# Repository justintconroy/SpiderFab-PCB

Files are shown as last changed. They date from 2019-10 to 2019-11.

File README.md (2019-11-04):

# SpiderFab Control Board

This board is made to control [SpiderFab](https://github.com/justintconroy/SpiderFab).

It's mostly just my attempts to learn how to make PCBs using EAGLE.
Version 1.0 supports:
* 2.3-16V battery power supply
* 1000mAh charger for internal LiPo battery
* Charge via USB or 5mm barrel connector
* 12 servos
* 2 DC motors

# Next version
I'm already thinking of what I might change on this to make it more
generally useful. Potential changes:
* Add a [GPIO expander](https://www.mouser.com/ProductDetail/NXP-Semiconductors/PCA9685PW118?qs=sGAEpiMZZMvKM5ialpXrmnWDpPMxsdrM)
  to support more actuators.
* Switch to an SMT version of the motor driver to make some more space
  on the board. (might be a bad idea if we want to make it easy to
  replace burned out drivers by socketing them).
* Add another motor driver to allow controlling 4 motors.

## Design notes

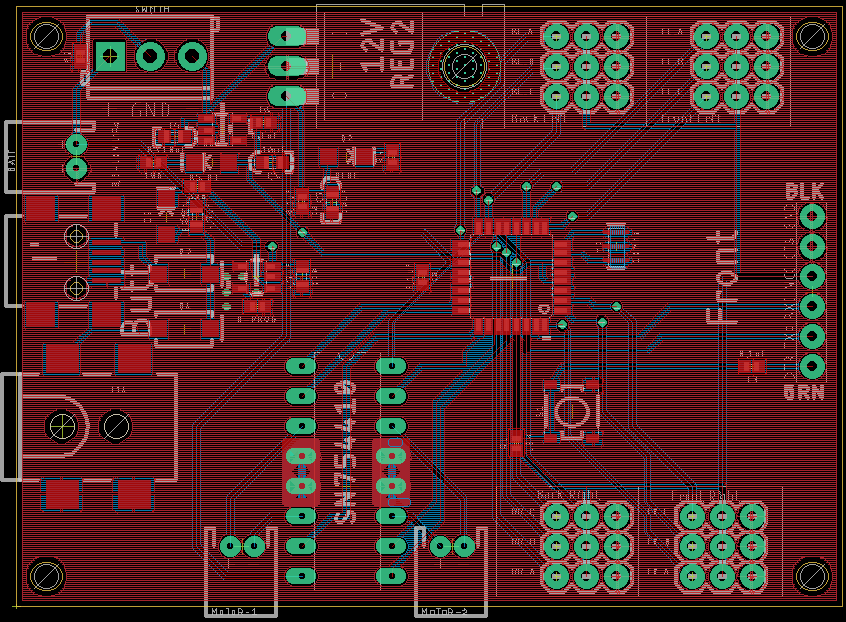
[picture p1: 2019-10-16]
SpiderFab_Board_Front.png

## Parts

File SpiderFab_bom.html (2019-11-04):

Qty | Value | Device | Package | Parts | Description | DESIGNER | PROD_ID | SF_ID | SKU | VALUE | VERSION
1 |  | 6_PIN_SERIAL_TARGETSILK | 6_PIN_SERIAL_TARGET_SIDE_W_SILK | J1 | 6-pin header connection for use with the "FTDI BASIC" pinout - TARGET SIDE.
2 |  | CONN_02JST-PTH-2 | JST-2-PTH | MOTOR-1, MOTOR-2 | Multi connection point. Often used as Generic Header-pin footprint for 0.1 inch spaced/style header connections |  | CONN-09863 |  | PRT-09914
12 |  | CONN_03 | 1X03 | BL_A, BL_B, BL_C, BR_A, BR_B, BR_C, FL_A, FL_B, FL_C, FR_A, FR_B, FR_C | Multi connection point. Often used as Generic Header-pin footprint for 0.1 inch spaced/style header connections
1 |  | CONN_03SCREW | SCREWTERMINAL-3.5MM-3 | SWITCH | Multi connection point. Often used as Generic Header-pin footprint for 0.1 inch spaced/style header connections |  | CONN-08288 | PRT-08235
2 |  | RESISTOR0402 | 0402 | R2, R4 | Generic Resistor Package
4 | 0.1uF | 0.1UF-0402-16V-10% | 0402 | C2, C3, C6, C8 | 0.1µF ceramic capacitors |  | CAP-12416 |  |  | 0.1uF
2 | 10K | RESISTOR0402 | 0402 | R1, R3 | Generic Resistor Package
3 | 10uF | 10UF-POLAR-0603-6.3V-20%(TANT) | 0603-POLAR | C4, C5, C7 | 10.0µF polarized capacitors |  | CAP-13210 |  |  | 10uF
1 | 12V | V_REG_78XX-TO-220 | TO-220-ALT | REG2 | Voltage Regulator |  | VREG-08450 | COM-00107
1 | 16MHz | RESONATOR-16MHZSMD_3.2X1.3 | RESONATOR-SMD-3.2X1.3 | Y1 | 16MHz Resonator |  | XTAL-08900 |  |  | 16MHz
2 | 1A/40V/500mV | DIODE-SCHOTTKY-SS14 | SMA-DIODE | D3, D4 | Schottky diode |  | DIO-08053 |  |  | 1A/40V/500mV
1 | 1K | RESISTOR0402 | 0402 | R-PROG | Generic Resistor Package
1 | 3.3-16V LiPo | CONN_02JST-PTH-2 | JST-2-PTH | BATT | Multi connection point. Often used as Generic Header-pin footprint for 0.1 inch spaced/style header connections |  | CONN-09863 |  | PRT-09914
1 | 3.3V/150mA | V_REG_MIC52053.3V | SOT23-5 | REG1 | V_REG MIC5205 Standard 3.3V, 5V, and Adjustable 150mA LDO voltage regulator in SOT-23 layout. Micrel part MIC5205. BP (by-pass) pin is used to lower output noise with 470pF cap, may be left open. On the adjustable version BP is used to set output. |  | VREG-00822 |  |  | 3.3V/150mA
1 | 330 | RESISTOR0402 | 0402 | R5 | Generic Resistor Package
2 | 4.7uF | 4.7UF0603 | 0603 | C9, C10 | 4.7µF ceramic capacitors |  | CAP-08280 |  |  | 4.7uF
1 | 5.5x2.1mm Barrel | POWER_JACKSMD | POWER_JACK_SMD | J14 | Power Jack Connector |  | CONN-08106 | PRT-12748 |  | 5.5x2.1mm Barrel
1 | ATMEGA328 | ATMEGA168 | TQFP32-08 | U1
1 | BLUE | LED1206 | LED-1206 | D2 | LED (Generic)
1 | FRAME-LETTERNO_PACKAGE | FRAME-LETTERNO_PACKAGE | DUMMY | FRAME1 | Schematic Frame - Letter | Justin T. Conroy |  |  |  |  | v01
1 | GREEN | LED1206 | LED-1206 | D5 | LED (Generic)
1 | MCP73831 | MCP73831 | SOT23-5 | U3 | Miniature single cell, fully integrated Li-Ion, Li-polymer charge management controller |  | IC-09995
1 | MOMENTARY-SWITCH-SPST-SMD-4.5MM | MOMENTARY-SWITCH-SPST-SMD-4.5MM | TACTILE_SWITCH_SMD_4.5MM | S1 | Momentary Switch (Pushbutton) - SPST |  | SWCH-09213
1 | RED | LED1206 | LED-1206 | D1 | LED (Generic)
1 | SN754410 | SN754410 | DIP16 | IC1 | Quadruple half-H driver
1 | USBSMD | USBSMD | USB-MINIB | X1 | USB Connectors

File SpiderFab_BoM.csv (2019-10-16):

Part | Value | Device | Package | Description | DESIGNER | PROD_ID | SF_ID | SKU | VALUE | VERSION
BATT | 3.3-16V LiPo | CONN_02JST-PTH-2 | JST-2-PTH | Multi connection point. Often used as Generic Header-pin footprint for 0.1 inch spaced/style header connections |  | CONN-09863 |  | PRT-09914
BL_A |  | CONN_03 | 1X03 | Multi connection point. Often used as Generic Header-pin footprint for 0.1 inch spaced/style header connections
BL_B |  | CONN_03 | 1X03 | Multi connection point. Often used as Generic Header-pin footprint for 0.1 inch spaced/style header connections
BL_C |  | CONN_03 | 1X03 | Multi connection point. Often used as Generic Header-pin footprint for 0.1 inch spaced/style header connections
BR_A |  | CONN_03 | 1X03 | Multi connection point. Often used as Generic Header-pin footprint for 0.1 inch spaced/style header connections
BR_B |  | CONN_03 | 1X03 | Multi connection point. Often used as Generic Header-pin footprint for 0.1 inch spaced/style header connections
BR_C |  | CONN_03 | 1X03 | Multi connection point. Often used as Generic Header-pin footprint for 0.1 inch spaced/style header connections
C2 | 0.1uF | 0.1UF-0402-16V-10% | 0402 | 0.1µF ceramic capacitors |  | CAP-12416 |  |  | 0.1uF
C3 | 0.1uF | 0.1UF-0402-16V-10% | 0402 | 0.1µF ceramic capacitors |  | CAP-12416 |  |  | 0.1uF
C4 | 10uF | 10UF-POLAR-0603-6.3V-20%(TANT) | 0603-POLAR | 10.0µF polarized capacitors |  | CAP-13210 |  |  | 10uF
C5 | 10uF | 10UF-POLAR-0603-6.3V-20%(TANT) | 0603-POLAR | 10.0µF polarized capacitors |  | CAP-13210 |  |  | 10uF
C6 | 0.1uF | 0.1UF-0402-16V-10% | 0402 | 0.1µF ceramic capacitors |  | CAP-12416 |  |  | 0.1uF
C7 | 10uF | 10UF-POLAR-0603-6.3V-20%(TANT) | 0603-POLAR | 10.0µF polarized capacitors |  | CAP-13210 |  |  | 10uF
C8 | 0.1uF | 0.1UF-0402-16V-10% | 0402 | 0.1µF ceramic capacitors |  | CAP-12416 |  |  | 0.1uF
C9 | 4.7uF | 4.7UF0603 | 0603 | 4.7µF ceramic capacitors |  | CAP-08280 |  |  | 4.7uF
C10 | 4.7uF | 4.7UF0603 | 0603 | 4.7µF ceramic capacitors |  | CAP-08280 |  |  | 4.7uF
D1 | RED | LED1206 | LED-1206 | LED (Generic)
D2 | BLUE | LED1206 | LED-1206 | LED (Generic)
D3 | 1A/40V/500mV | DIODE-SCHOTTKY-SS14 | SMA-DIODE | Schottky diode |  | DIO-08053 |  |  | 1A/40V/500mV
D4 | 1A/40V/500mV | DIODE-SCHOTTKY-SS14 | SMA-DIODE | Schottky diode |  | DIO-08053 |  |  | 1A/40V/500mV
D5 | GREEN | LED1206 | LED-1206 | LED (Generic)
FL_A |  | CONN_03 | 1X03 | Multi connection point. Often used as Generic Header-pin footprint for 0.1 inch spaced/style header connections
FL_B |  | CONN_03 | 1X03 | Multi connection point. Often used as Generic Header-pin footprint for 0.1 inch spaced/style header connections
FL_C |  | CONN_03 | 1X03 | Multi connection point. Often used as Generic Header-pin footprint for 0.1 inch spaced/style header connections
FRAME1 | FRAME-LETTERNO_PACKAGE | FRAME-LETTERNO_PACKAGE | DUMMY | Schematic Frame - Letter | Justin T. Conroy |  |  |  |  | v01
FR_A |  | CONN_03 | 1X03 | Multi connection point. Often used as Generic Header-pin footprint for 0.1 inch spaced/style header connections
FR_B |  | CONN_03 | 1X03 | Multi connection point. Often used as Generic Header-pin footprint for 0.1 inch spaced/style header connections
FR_C |  | CONN_03 | 1X03 | Multi connection point. Often used as Generic Header-pin footprint for 0.1 inch spaced/style header connections
IC1 | SN754410 | SN754410 | DIP16 | Quadruple half-H driver
J1 |  | 6_PIN_SERIAL_TARGETSILK | 6_PIN_SERIAL_TARGET_SIDE_W_SILK | 6-pin header connection for use with the FTDI BASIC" pinout - TARGET SIDE."
J14 | 5.5x2.1mm Barrel | POWER_JACKSMD | POWER_JACK_SMD | Power Jack Connector |  | CONN-08106 | PRT-12748 |  | 5.5x2.1mm Barrel
MOTOR-1 |  | CONN_02JST-PTH-2 | JST-2-PTH | Multi connection point. Often used as Generic Header-pin footprint for 0.1 inch spaced/style header connections |  | CONN-09863 |  | PRT-09914
MOTOR-2 |  | CONN_02JST-PTH-2 | JST-2-PTH | Multi connection point. Often used as Generic Header-pin footprint for 0.1 inch spaced/style header connections |  | CONN-09863 |  | PRT-09914
R-PROG | 1K | RESISTOR0402 | 0402 | Generic Resistor Package
R1 | 10K | RESISTOR0402 | 0402 | Generic Resistor Package
R2 |  | RESISTOR0402 | 0402 | Generic Resistor Package
R3 | 10K | RESISTOR0402 | 0402 | Generic Resistor Package
R4 |  | RESISTOR0402 | 0402 | Generic Resistor Package
R5 | 330 | RESISTOR0402 | 0402 | Generic Resistor Package
REG1 | 3.3V/150mA | V_REG_MIC52053.3V | SOT23-5 | V_REG MIC5205 Standard 3.3V, 5V, and Adjustable 150mA LDO voltage regulator in SOT-23 layout. Micrel part MIC5205. BP (by-pass) pin is used to lower output noise with 470pF cap, may be left open. On the adjustable version BP is used to set output. |  | VREG-00822 |  |  | 3.3V/150mA
REG2 | 12V | V_REG_78XX-TO-220 | TO-220-ALT | Voltage Regulator |  | VREG-08450 | COM-00107
S1 | MOMENTARY-SWITCH-SPST-SMD-4.5MM | MOMENTARY-SWITCH-SPST-SMD-4.5MM | TACTILE_SWITCH_SMD_4.5MM | Momentary Switch (Pushbutton) - SPST |  | SWCH-09213
SWITCH |  | CONN_03SCREW | SCREWTERMINAL-3.5MM-3 | Multi connection point. Often used as Generic Header-pin footprint for 0.1 inch spaced/style header connections |  | CONN-08288 | PRT-08235
U1 | ATMEGA328 | ATMEGA168 | TQFP32-08
U3 | MCP73831 | MCP73831 | SOT23-5 | Miniature single cell, fully integrated Li-Ion, Li-polymer charge management controller |  | IC-09995
X1 | USBSMD | USBSMD | USB-MINIB | USB Connectors
Y1 | 16MHz | RESONATOR-16MHZSMD_3.2X1.3 | RESONATOR-SMD-3.2X1.3 | 16MHz Resonator |  | XTAL-08900 |  |  | 16MHz

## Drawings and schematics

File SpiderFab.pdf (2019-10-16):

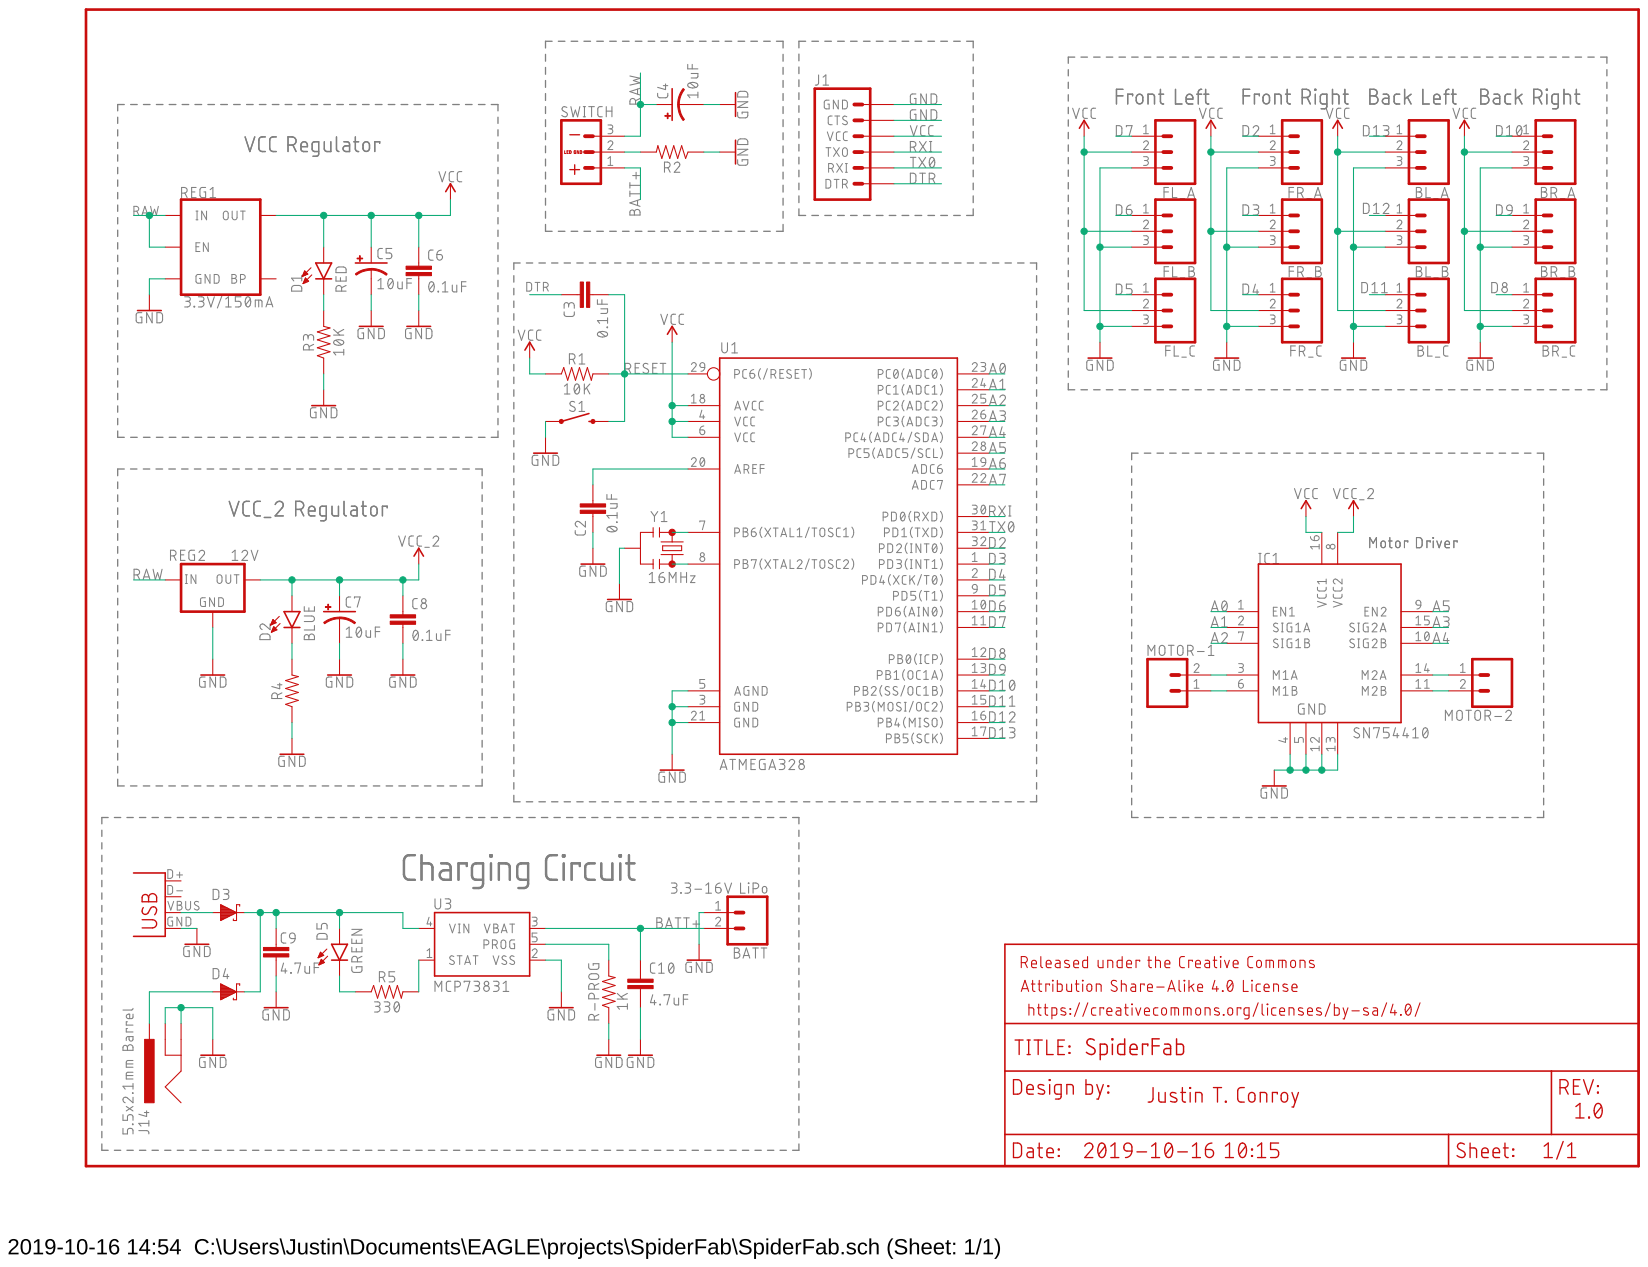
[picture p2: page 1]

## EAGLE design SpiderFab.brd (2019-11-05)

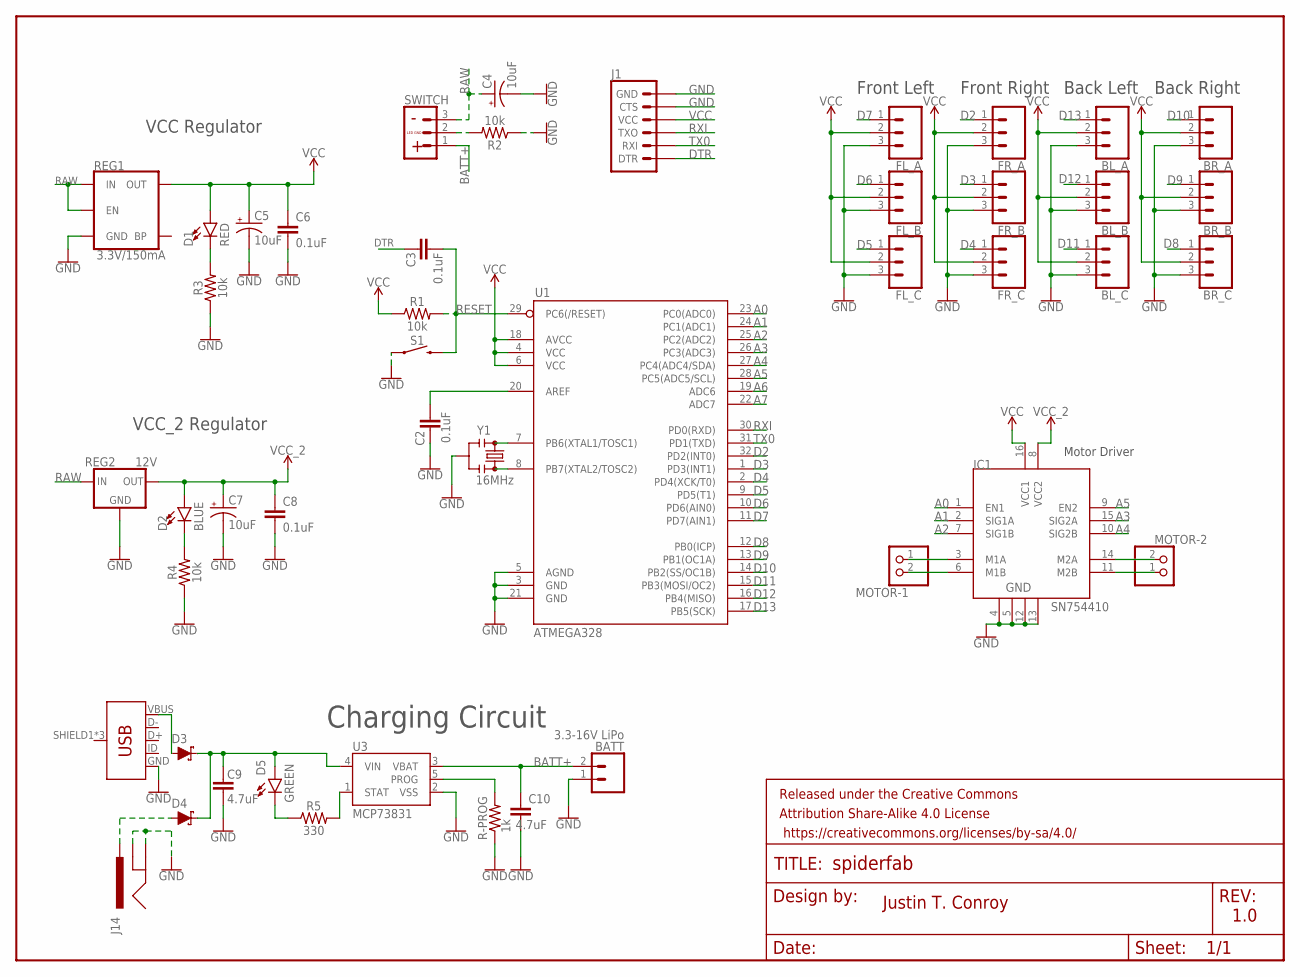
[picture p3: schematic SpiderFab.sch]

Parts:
BATT: 3.3-16V LiPo; JST-2-PTH
BL_A: CONN_03; 1X03
BL_B: CONN_03; 1X03
BL_C: CONN_03; 1X03
BR_A: CONN_03; 1X03
BR_B: CONN_03; 1X03
BR_C: CONN_03; 1X03
C2: 0.1uF; 0402
C3, C6, C8: 0.1uF; 0603
C4, C5, C7: 10uF; 0603-POLAR
C9, C10: 4.7uF; 0603
D1: RED; LED-1206
D2: BLUE; LED-1206
D3: 1A/40V/500mV; SOD-323
D4: 1A/40V/500mV; SMA-DIODE
D5: GREEN; LED-1206
FL_A: CONN_03; 1X03
FL_B: CONN_03; 1X03
FL_C: CONN_03; 1X03
FRAME1: FRAME-LETTERNO_PACKAGE; DUMMY
FR_A: CONN_03; 1X03
FR_B: CONN_03; 1X03
FR_C: CONN_03; 1X03
IC1: SN754410; DIP16
J1: 6_PIN_SERIAL_TARGETSILK; 6_PIN_SERIAL_TARGET_SIDE_W_SILK
J14: POWER_JACK; POWER_JACK_PTH
MOTOR-1, MOTOR-2: JST_2PIN-THM; JST-PH-2-THM
R1, R2, R3, R4: 10k; 0603
R5: 330; 0603
R-PROG: 1k; 0603
REG1: 3.3V/150mA; SOT23-5
REG2: 12V; TO-220-ALT
S1: MOMENTARY-SWITCH-SPST-SMD-4.5MM; TACTILE_SWITCH_SMD_4.5MM
SWITCH: CONN_03JST-PTH-VERT; JST-3-PTH-VERT
U1: ATMEGA328; TQFP32-08
U3: MCP73831; SOT23-5
X1: AMP FCI 10103594-0001LF; USB-B-MICRO-SMD
Y1: 16MHz; RESONATOR-SMD-3.2X1.3

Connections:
A0: IC1.1 (EN1), U1.23 (PC0(ADC0))
A1: IC1.2 (SIG1A), U1.24 (PC1(ADC1))
A2: IC1.7 (SIG1B), U1.25 (PC2(ADC2))
A3: IC1.15 (SIG2A), U1.26 (PC3(ADC3))
A4: IC1.10 (SIG2B), U1.27 (PC4(ADC4/SDA))
A5: IC1.9 (EN2), U1.28 (PC5(ADC5/SCL))
A6: U1.19 (ADC6)
A7: U1.22 (ADC7)
BATT+: BATT.2, C10.1, SWITCH.1, U3.3 (VBAT)
D2: FR_A.1, U1.32 (PD2(INT0))
D3: FR_B.1, U1.1 (PD3(INT1))
D4: FR_C.1, U1.2 (PD4(XCK/T0))
D5: FL_C.1, U1.9 (PD5(T1))
D6: FL_B.1, U1.10 (PD6(AIN0))
D7: FL_A.1, U1.11 (PD7(AIN1))
D8: BR_C.1, U1.12 (PB0(ICP))
D9: BR_B.1, U1.13 (PB1(OC1A))
D10: BR_A.1, U1.14 (PB2(SS/OC1B))
D11: BL_C.1, U1.15 (PB3(MOSI/OC2))
D12: BL_B.1, U1.16 (PB4(MISO))
D13: BL_A.1, U1.17 (PB5(SCK))
DTR: C3.1, J1.P$1 (DTR)
GND: BATT.1, BL_A.3, BL_B.3, BL_C.3, BR_A.3, BR_B.3, BR_C.3, C2.2, C4.-, C5.-, C6.2, C7.-, C8.2, C9.2, C10.2, FL_A.3, FL_B.3, FL_C.3, FR_A.3, FR_B.3, FR_C.3, IC1.4, IC1.5, IC1.12, IC1.13, J1.P$5 (CTS), J1.P$6 (GND), J14.GND, J14.GNDBREAK, R2.1, R3.1, R4.1, R-PROG.1, REG1.2 (GND), REG2.GND, S1.2 (1), S1.3 (1), U1.3 (GND), U1.5 (AGND), U1.21 (GND), U3.2 (VSS), X1.GND, Y1.2
unnamed: U1.7 (PB6(XTAL1/TOSC1)), Y1.1
unnamed: U1.8 (PB7(XTAL2/TOSC2)), Y1.3
unnamed: IC1.3 (M1A), MOTOR-1.1 (2)
unnamed: C2.1, U1.20 (AREF)
unnamed: IC1.6 (M1B), MOTOR-1.2 (1)
unnamed: IC1.14 (M2A), MOTOR-2.2 (1)
unnamed: IC1.11 (M2B), MOTOR-2.1 (2)
unnamed: D3.A, X1.VBUS
unnamed: D4.A, J14.PWR
unnamed: D2.C, R4.2
unnamed: R2.2, SWITCH.2
unnamed: D1.C, R3.2
unnamed: C9.1, D3.C, D4.C, D5.A, U3.4 (VIN)
unnamed: D5.C, R5.1
unnamed: R5.2, U3.1 (STAT)
unnamed: R-PROG.2, U3.5 (PROG)
RAW: C4.+, REG1.1 (IN), REG1.3 (EN), REG2.IN, SWITCH.3
RESET: C3.2, R1.2, S1.1 (2), S1.4 (2), U1.29 (PC6(/RESET))
RXI: J1.P$2 (TXO), U1.30 (PD0(RXD))
TX0: J1.P$3 (RXI), U1.31 (PD1(TXD))
VCC: BL_A.2, BL_B.2, BL_C.2, BR_A.2, BR_B.2, BR_C.2, C5.+, C6.1, D1.A, FL_A.2, FL_B.2, FL_C.2, FR_A.2, FR_B.2, FR_C.2, IC1.16 (VCC1), J1.P$4 (VCC), R1.1, REG1.5 (OUT), U1.4 (VCC), U1.6 (VCC), U1.18 (AVCC)
VCC_2: C7.+, C8.1, D2.A, IC1.8 (VCC2), REG2.OUT

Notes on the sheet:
Front Left
Front Right
Back Left
Back Right
Motor Driver
Charging Circuit
VCC Regulator
VCC_2 Regulator
Justin T. Conroy
1.0
LED GND

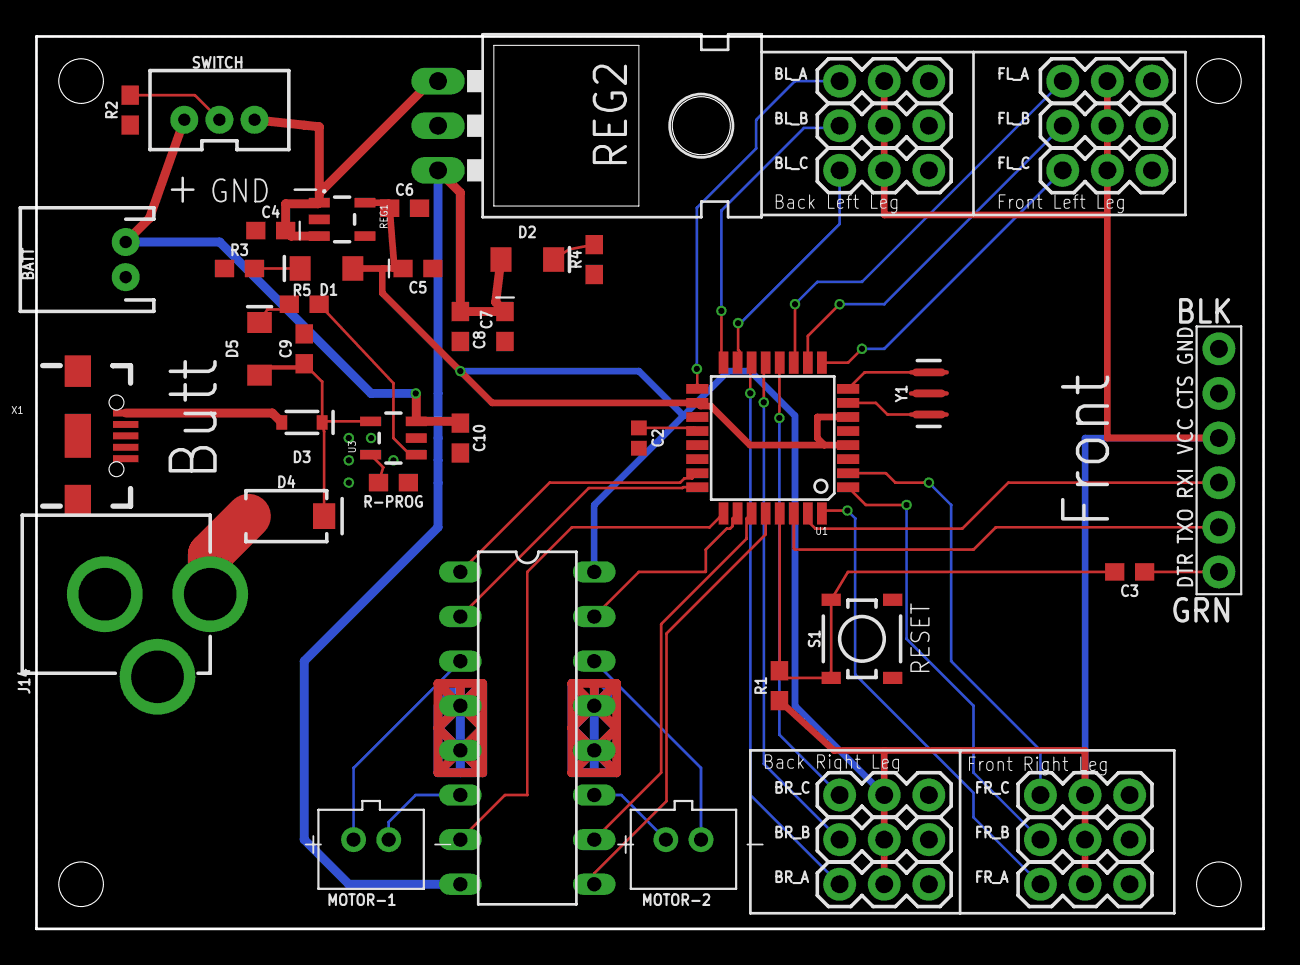
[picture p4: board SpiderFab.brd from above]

Board: 2 copper layers, 69.8 x 50.8 mm, 47 parts (0 on the bottom side), 43 nets.

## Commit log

2019-10-16 Initial commit.
    V1 of the SpiderFab board. Supports 12 servos and 2 DC motors.
    [SpiderFab.brd, SpiderFab.sch, SpiderFab_BoM.csv]
2019-10-31 Make power traces thicker.
    [SpiderFab.brd]
2019-11-04 Label RESET button on the silkscreen.
    Also adds a couple versions of the BoM.
    [SpiderFab.brd]
2019-11-04 Swap 0402 caps for 0603 package.
    [SpiderFab.brd, SpiderFab.sch]
2019-11-04 Change footprint for diodes and resistors.
    [SpiderFab.brd, SpiderFab.sch]
2019-11-04 Replace internal connectors with vertical JST.
    [SpiderFab.brd, SpiderFab.sch]
2019-11-05 Swap some components for a different package.
    [SpiderFab.brd, SpiderFab.sch]

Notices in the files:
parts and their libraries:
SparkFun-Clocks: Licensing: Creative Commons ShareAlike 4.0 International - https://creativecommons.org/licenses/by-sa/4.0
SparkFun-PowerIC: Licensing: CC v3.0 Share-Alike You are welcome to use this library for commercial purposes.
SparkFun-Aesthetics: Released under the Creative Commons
